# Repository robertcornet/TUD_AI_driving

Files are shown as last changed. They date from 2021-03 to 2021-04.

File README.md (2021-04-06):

# TU Delft AI driving platform
Here you can learn everything about the TU Delft AI driving platform. It is designed for the department of Cognitive Robotics (CoR) at the faculty of 3ME at the TU Delft.

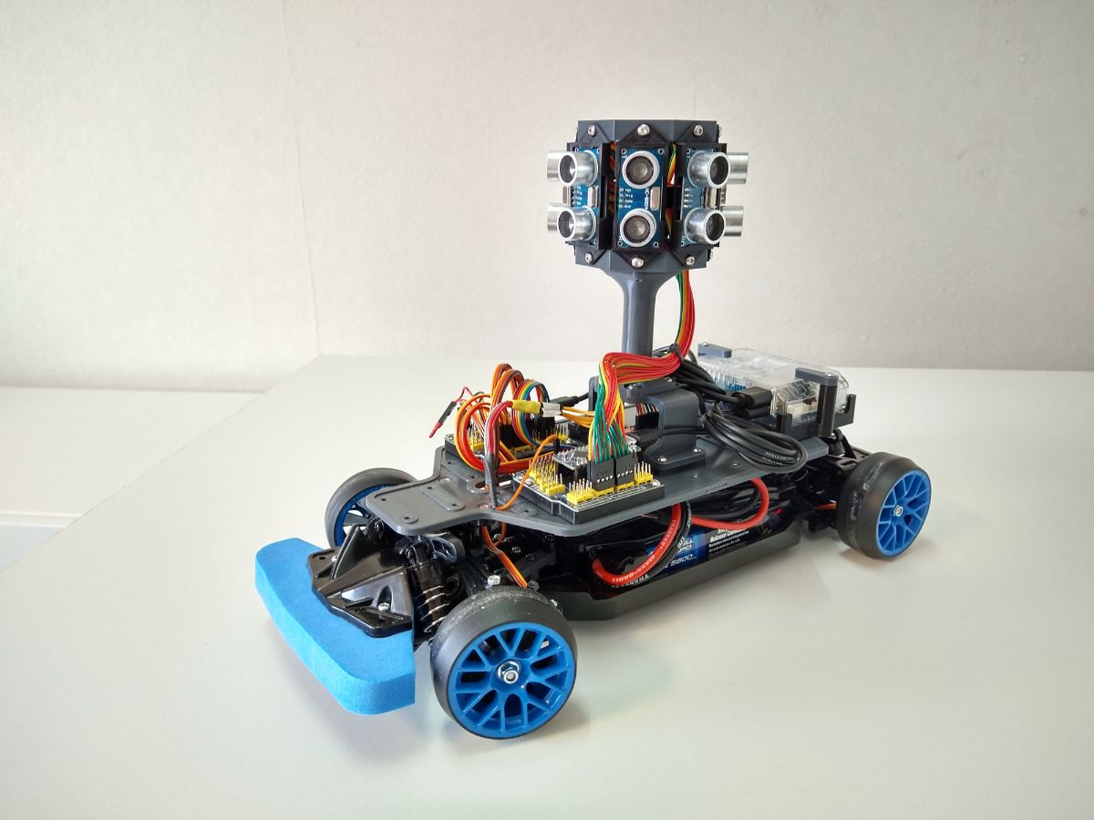
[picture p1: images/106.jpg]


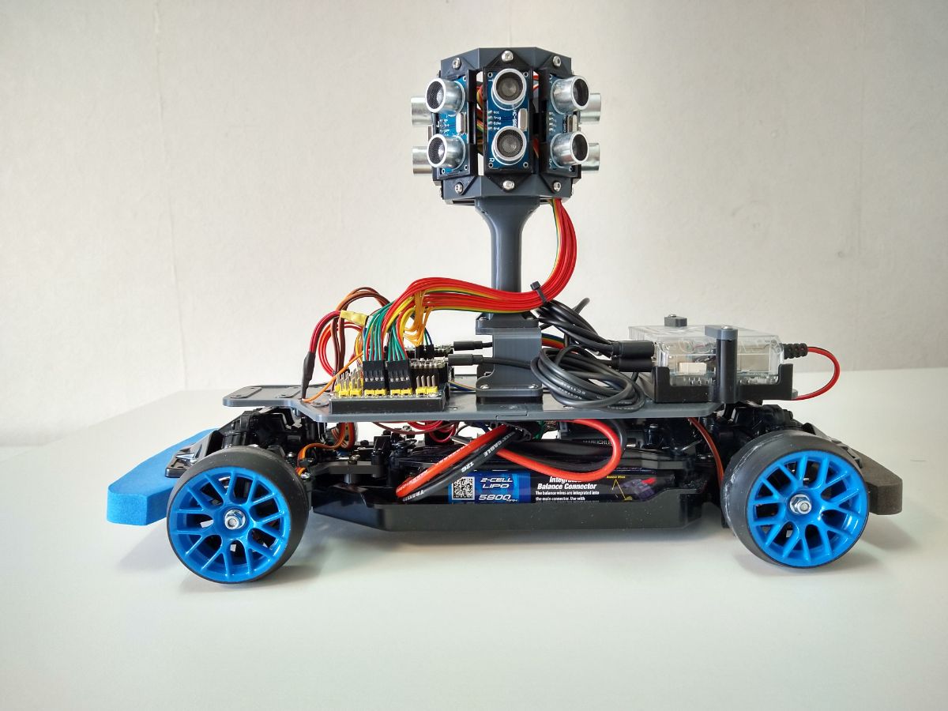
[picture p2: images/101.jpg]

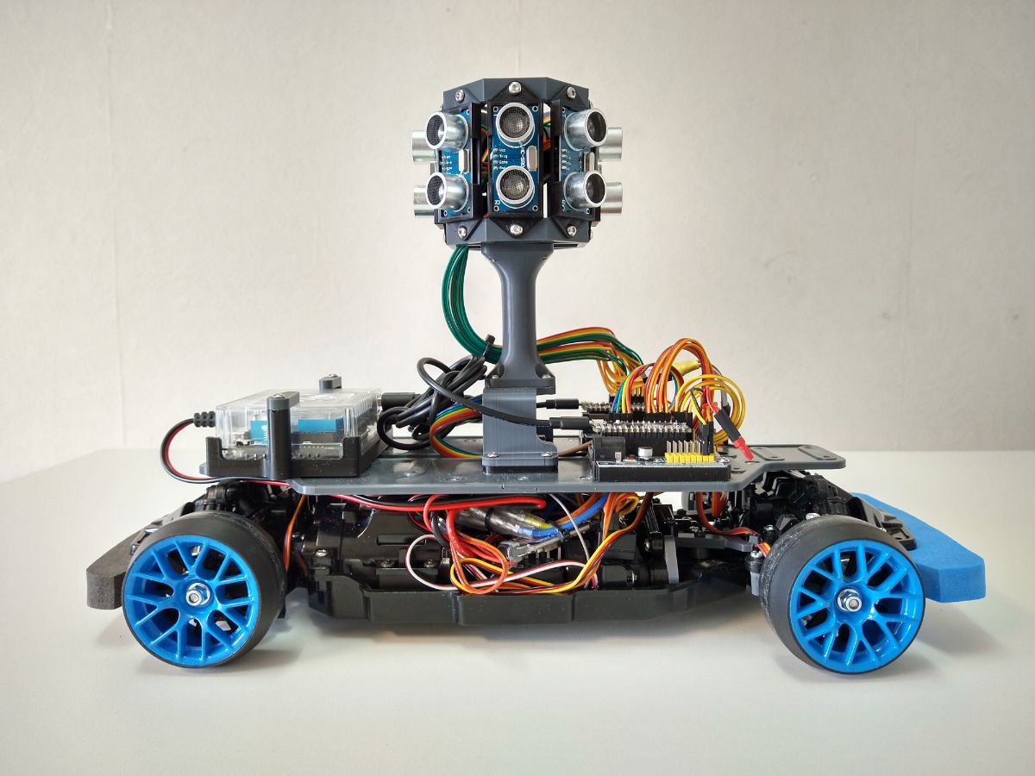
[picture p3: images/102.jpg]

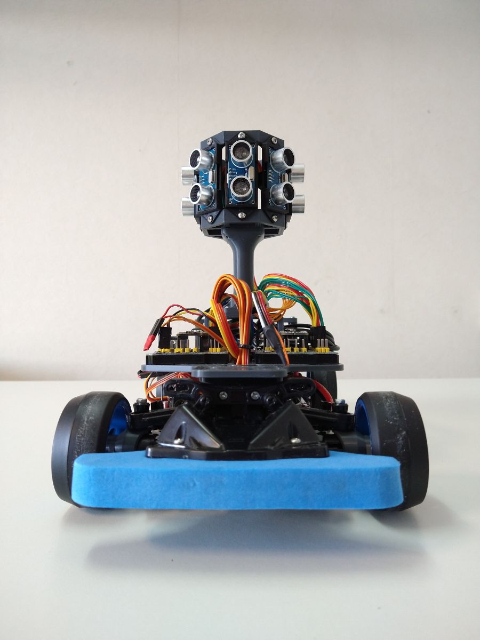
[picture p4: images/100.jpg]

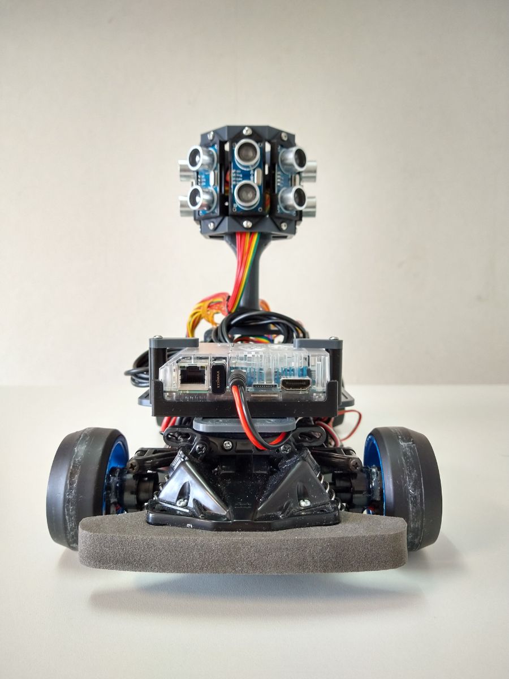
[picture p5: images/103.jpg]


## Who is it for?
This car is designed for very dynamic driving tasks, such as drifting. It can show the unstable behaviour of cars that are pushed to the limit of friction, at low speed and in small spaces. 

With a simple change of tires, you can convert it to a fast (30 km/h) and stable car.

If you are into vehicle research that goes beyond navigation tasks and focusses on dynamic vehicle behaviour and vehicle stability, this platform can be for you. It offers the dynamics of large research platforms on a small scale that requires little space. The onboard accelerometers, gyros and individual wheel speed sensors provide a good basis for developing impressive vehicle controllers.

## What does it offer?
- Low-cost dynamic driving
- Small scale for indoor use
- Access to the relevant vehicle states. (wheel speeds, accelerations, yaw rate)
- Onboard TensorFlow integration for AI development
- Modular platform for easy addition of your own sensors

## Getting Started
- Order everything you need from the [Bill of Materials](/documentation/bill_of_materials.md) 
- Print the [CAD models](/cad)
- Assemble your car with the help of the [Build Guide](/documentation/build_guide.md)
- Install the [Software](/documentation/software_setup.md)

Your platform should now be ready to begin! 
If you want some extra help, check out the [Operation Manual](/documentation/operation_manual.md). If you want to build a vehicle simulation to train your AI, check out the [Simulator section](/simulator).

## See Also
- [BARC](https://github.com/MPC-Berkeley/barc)
- [NVIDIA JetRacer](https://github.com/NVIDIA-AI-IOT/jetracer)
- [AutoRally](https://autorally.github.io/)
- [DonkeyCar](https://www.donkeycar.com/)

## To Do
- Try filtering IMU Data. _The IMU is polled 10-100x faster than the results are published. Try taking the average of all measurements in the publishing interval. _
- Large steering angle mod. _For rear wheel drive drifting, a large steering angle is needed to balance the vehicle in the drift._
- Camera Vision / Lidar module. _The usability of the Ultrasonic sensors is limited._
- Better Inertial Navigation. _Robust algorithm to determine vehicle orientation in space._
- Standstill vehicle rotating bug. _In the simulator, if the vehicle is stationary, it can rotate slowly by steering. This is due to how the slip angles are defined._

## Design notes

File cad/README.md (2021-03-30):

# CAD

The STL files in this folder are meant to be 3D printed. Do not forget to cut the threads for the M3 bolt holes!

The main frame is split into two parts (front and rear) so it can be printed with a smaller printbed.

# Expirimental

In the expirimental folder, you can find the parts that will increase the steering angle from 16.5 degrees (standard) to an average of 29 degrees. 
You can only use this if the front driveshafts are removed.

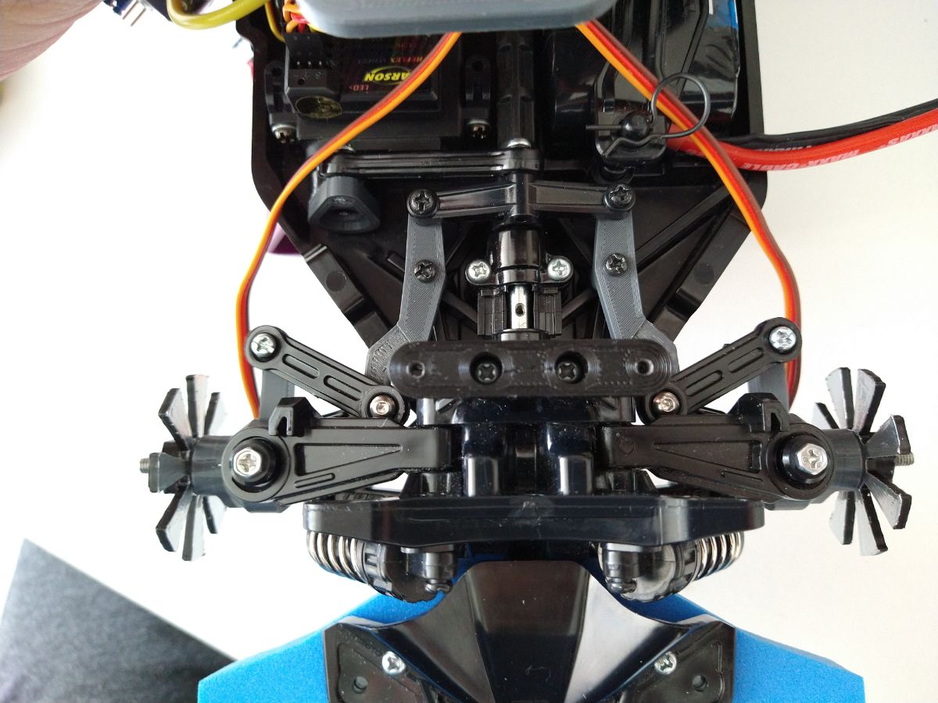
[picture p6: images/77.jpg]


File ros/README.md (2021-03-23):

# How it works
The provided ROS package has very few components. Our network has 3 'nodes', and we can send messages between these nodes.  
- Node 1: This node is on Arduino 1, and sends messages over USB with the topic 'vehicle_state'. It also listens to the messages from Node 3 with the topic 'control_actions'.  
- Node 2: This node is on Arduino 2, and sends messages over USB with the topic 'radar_state'.  
- Node 3: This is the controller that runs on the computer. It listens to Nodes 1 and 2 about the 'vehicle_state' and 'radar_state'. Based on this information, it sends the 'control_actions' to Node 1.

The Arduinos are set to publish a new message with a frequency of 25 hz (40ms interval).

# Setting up your ROS environment
After installing ROS, start by [setting up your own workspace.](http://wiki.ros.org/ROS/Tutorials/InstallingandConfiguringROSEnvironment) The name of the workspace attached is 'tu_ws'.

There are only a few components needed to get the car running. These are:
- custom messages. The vehicle_state_msg and radar_state_msg messages are simple custom messages that tell us what kind of data we can expect on the vehicle_state and radar_state topics.
- launch file: A launch file makes it easy to start multiple processes in one go. We use it to start the two USB connections to the Arduinos.
- script: A script is a function or program we can run on a ROS node. In our case, *controller.py* is the script were we keep our controller.

The above is all captured in a 'package', called *car*.

# TOPICS
vehicle_state
radar_state
control_actions
# MESSAGES

## vehice_state_msg
- float32 u (m/s)
- float32 v (m/s)
- float32 r (rad/s)
- float32 a_x (m/s^2)
- float32 a_y (m/s^2)		
- float32 omega_fl (rad/s)
- float32 omega_fr (rad/s)
- float32 omega_rl (rad/s)
- float32 omega_rr (rad/s)
		
## radar_state_msg
- float32 radar1 (left)(cm)
- float32 radar2
- float32 radar3
- float32 radar4
- float32 radar5
- float32 radar6
- float32 radar7
- float32 radar8 (right)

## control_actions_msg
- float32 steering_action ([-1,1])
- float32 throttle_action ([-1,1])

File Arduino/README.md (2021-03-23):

# Arduino
The sensors on the vehicle are connected to 2 Arduino Nano's. The Arduinos publish the sensor information over USB on the ROS network. They also receive the steering and throttle commands from the ROS network.

## Arduino 1 - Vehicle sensors
The first Arduino is wired to all the vehicle specific sensors:

- Inertial Measurement Unit (IMU)
- Wheel speed sensors (4x)
- 3 Channel RC receiver 

Every 40 milliseconds the sensor information is published on the ROS network.

This Arduino also controls the actuators:
- Steering out (servo)
- Throttle out (esc)

For the Throttle and Steering actions you can switch between two sources:
- Actions from the RC receiver (manual control)
- Actions from the ROS network (automated mode)

## Arduino 2 - Ultrasonic sensors
The second Arduino is for the ultrasonic sensors. There are 2 files included that use the sensors in a different way.

### radar_parallel.ino
In this file, all sensors are triggered at the same time:

> every 40 ms:  
> *publish latest sensor values on ROS network*    
> *trigger all sensors simultaneously*

### radar_sequential.ino
In this file, a sensor is triggered after the previous sensor is finished:

> trigger sensor n  
>   
> *if* (response received or timeout expired (no response received)){  
>      *trigger sensor n+1*  
> }

> every 40 ms:  
> *publish latest sensor values on ROS network*

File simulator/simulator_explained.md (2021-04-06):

# Vehicle motion simulator

The simulator can be used to develop and test your controllers. From the two inputs (Steering and Throttle), it will approximate how the car would behave. The simulator is built in the [OpenAI GYM](https://gym.openai.com/) structure.

The simulator is used in combination with the Reinforcement Learning programs from the [RLControlTheoreticGuarantee Github](https://github.com/RLControlTheoreticGuarantee/Guarantee_Learning_Control). 

Inluded on this page is a folder with an older copy of that github, including the vehicle simulator. 
If you follow their installation guide, you can download the folder above and start training immediately.

## Using the simulator
- Define your objective and what states you can observe in your experiment. Make sure your controller does not rely on states that you can not observe in the real world!
- Choose the time step for the agent (eg, 10 hz, 25hz, etc). The vehicle simulation updates at 1000hz for stable integration. 
- Define how you want an episode to start (*def* reset) and when to end (*done*)
- Construct your reward so it promotes the desired behaviour

## States
In the simulator you have access to the following vehicle states:

- longitudinal velocity *u*
- lateral velocity *v*
- yaw rate *r*
- longitudinal acceleration *a<sub>x</sub>*
- lateral acceleration *a<sub>y</sub>*
- wheel rotation velocities *Ω* 

Additionally, you can generate environment borders: \
- As a random racetrack
- As a square room

These borders can be detected with a 'lidar' simulation.

## Primary Simulator Functions
The most important functions are:

*def* \_\_init\_\_()\
Here all the parameters are set for the car and the environment. For example, here you would change the mass, the dimensions, or the motor characteristics of the car. This is also were you set if your car is 4wd or rwd, and how large the time steps of the simulation will be.

*def* reset()\
This function is called at the beginning of every training episode. It (re)sets the parameters for the episode. Here you can set how and where your vehicle starts in the environment. It can also be used to build a different enviroment for every episode.

*def* step()\
This is the main simulation function. It takes two inputs (steering and throttle), and runs the simulation for one step in the environment.  
It returns the new state of the car and environment, and a reward based on that state. 

## Secondary Simulator functions

*def* render()\
When eval_render == True in variant.py, this function is called every step. It draws the car and the environment.

### Motor and ESC
*def* ESC()\
This function simulates the behaviour of the electronic speed controller (ESC) included in the Tamiya kit (TBLE-02S).\
The ESC puts out a voltage to the motor depending on the input signal. The input is a PWM signal with pulses between 1000us (full throttle) and 2000us (full braking). This behaviour is modelled in the simulator as a voltage multiplier; the ESC acts as a multiplier in range [0-1] between the battery voltage and motor.\
The folling values were measured by experiment:

|Throttle %|Voltage Mult.|
|---|---|
|0|0|
|7.5|0|
|7.6|0.44|
|10|0.53|
|20|0.75|
|30|0.84|
|40|0.89|
|50|0.94|
|60|0.96|
|70|1|
|80|1|
|90|1|
|100|1|

*def* motor()\
This function calculates the torque that the motor will produce, given the voltage from the ESC and its rotational speed.

Tamiya specifies a motor RPM per volt (KV) of 2222, and a stall torque per volt (TV) of 0.0042 Nm. Our measurements revealed a KV closer to 2775, and a TV of 0.0065 Nm.

|Voltage|Motor RPM|KV|
|---|---|---|
|3.45|9322|2702|
|4.09|11376|2781|
|5.82|16116|2769|
|6.57|18179|2765|
|6.95|19276|2774|
|7.30|20540|2813|
|7.48|20935|2798|
|7.79|21725|2789|

### Tires
TIRE_FLUCTUATION is an array of 4 values. It can be used to add a little noise on the tire behaviour of the individual wheels, that changes from episode to episode.

### LIDAR
*def* lidar_get_state()\
Returns the distance to the walls at the angles set in SENSOR_ARRAY (*def* \_\_init\_\_()).\
*def* lidar_get_state() calls *def* lidar_rayDist(). There the distances can be checked in two different ways:
1. To the walls of a room (self.track__center)
2. To the 'walls' of a race track (self.track_left, self.track_right)\
Both options are quite different, make sure to uncomment the right one!

### Room generation
*def* gen_room()\
Very simple function that generates a square room given a length and width in meters. It returns the x,y-coordinates of the corners.

### Track generation
*def* track_generator()\
Generates a random track. It is adapted from the methods discussed [here](http://blog.meltinglogic.com/2013/12/how-to-generate-procedural-racetracks/)

*def* track_check_valid()\
Checks if the generated random track is 'valid'. If a track has 'kinks' in the corners, the track will be 'invalid'. 

## Expirimental, not recommended.

### Car following, leading car
These functions are for running a leading car. You can use it to train your AI to follow a car using lidar or ultrasonic sensing.

*def* initialize_leading_car()\
Initializes the leading car in a random position in front of your own car.

*def* run_leading_car()\
Chooses the actions for the leading car. Limits for the speed, acceleration and yaw rate of the leading car are set in this function.

*def* get_radar_state_zones()\
This function tries to simulate how an ultrasonic sensor would see the leading car in practice. If the leading car is within the FOV of a sensor, it returns the distance between the two cars.  

## See also
For more details of the vehicle motion simulation, refer to Chapter 2 of [this Thesis](https://repository.tudelft.nl/islandora/object/uuid%3A7bedb60a-ced8-4fcf-97ca-80208861a413)

# Learning Algorithms
With the included software, you can train your AI using Soft Actor Critic (SAC) and Lyapunov-based Soft Actor Critic (LSAC). Only the most basic settings will be discussed here.

variant.py\
Here you choose your environment, learning algorithm and training times. You can also set if you want to render the environment. 

main_for_sac.py\
This is the function you will run every time you want to start training or evaluating.

/LSAC/LSAC_V1.py\
Here you can change the dimensions of the neural networks. Change the following lines:
- lines 305/306
- lines 340/345
- lines 351/356

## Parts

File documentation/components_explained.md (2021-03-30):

# Componenents Explained

This page explains the choice of individual components, as well as how they are used, and what can be improved.

## The wheel speed sensors 
The rotational velocity of the wheels is important information when vehicle dynamics are considered. It is often the only measurement we have of the interface between the vehicle and the road.
It can be used to determine the velocity of the vehicle (from the non-driven wheels) or to estimate the longitudinal slip of the driven wheels.

Conventionally, wheel speeds are measured with hall sensors and a magnetic ring. This is also the method used on a large research platform such as the [AutoRally project](https://autorally.github.io/).

In our case, the rotational velocity is measured with IR-reflectance sensors. A small IR transmitter and receiver board is mounted on each wheel hub. A disk is mounted inside the wheels with aluminium tape to reflect the IR light. The gaps in the disk obviously do not reflect light, generating a square wave signal when the wheel is rotating.

IR-reflectance sensors can typically be bought in a **'Digital'** or **'Analog'** version. 
A digital sensor determines the reflectivity of a surface by pulling a voltage to 'HIGH', and counting how long it takes to discharge a small capacitor due to the amount of light reflected. This is a very slow process, and this gives no information about when the surface switches from 'light' to 'dark'. 

A much better solution is to use an **Analog** version of the board. An analog board puts out a voltage as a function of the reflected light. Since we are only interested in 'light' or 'dark', we can read the sensor with a **DIGITAL** pin on the arduino. Whenever the surface switches from **'light' to 'dark',** the voltage switches from **HIGH to LOW**, and an Interrupt routine is called to note the time of the switch.

Other projects use encoder disks with a black and white pattern to create a 'light' and 'dark' surface. This is not sufficient; a dark colored surface can still reflect IR light. A much more robust 'dark' surface is a surface that is sufficiently far away, regardless of color. Therefor a robust solution was found in using 'slotted' encoder disks.

An analog board with a **47k** resistor works best. Boards with a lower resistance will not reliable pull the voltage low enough to trigger Arduino's Digital LOW threshold.

## IMU

The vehicle is equiped with a low-cost 9-dof IMU:[SparkFun 9DoF IMU Breakout - ICM-20948](https://www.sparkfun.com/products/15335). 

This is used to measure the longitudinal and lateral accelerations.
The accelerations are measured in a plane perpendicular to gravitation vector. The orientation of the board is determined by a switching filter. This compensates the drift of the gyros and the noise of the accelerometers.

### Switching Filter	
If no motion is detected for a certain amount of time, the board is assumed to be stationary.
If the board is stationary; the orientation is determined by a weighted sum between the Accelerometers and the Gyrometers:

alpha = 0.95*(Gyro)+0.05*(Accel.)

When the board is in motion, the accelerometer data can no longer be used to accuratelyseperate the direction of the gravitational vector and the specific motion of the board. The angle is then solely determined by the Gyrometers:

alpha = 1.0*(Gyro)

### Inertial Navigation
The longitudinal and lateral velocity can be obtained by integrating the measured accelerations. In practice the usability of the calculated velocities is extremely limited. The calculated values are transmitted on the ROS network, but it is recommended that they should not be trusted.

## POWER
Power is supplied to the odroid with a 6 amp BEC(battery Eliminating Circuit). This is a common component in the RC hobby. Alternatively any DC/DC converter buck can be used that outputs 5V at 4+ A.

## Batteries
Power is provided to the car with Traxxas Lipo Batteries. They are very common, and easy to charge and maintain with plug and play chargers.

Do not let the voltage get too low. The vehicle will drain the battery completely if it is not disconnected. The battery monitor on the vehicle provides a reference for the voltage. If the voltage gets too low, the alarm will sound. 
The individual cell voltage can not be measured, only the sum (total voltage) is valid.

## Ultrasonic sensors
Ultrasonic sensors are used as a cheap way to observe the environment as an alternative to using camera vision. 

The vehicle can be equipped with a number of ultrasonic sensors in different configurations. The intention was to use ultrasonic sensors as a low cost alternative to lidar sensors. However, in testing it turns out that the usability of ultrasonic sensors is limited:

1. If the sensor is not pointing perpendicular to the surface it is supposed to measure, the sound waves will not bounce back to the receiver and the surface will not be observed correctly.

2. The relative slow speed of sound means that the sensors can not be polled at rates over 30hz. Normally, each sensor is polled individually, and the next sensor in the array is polled only after the first has received its echo (or has timed out). This would slow the update rate down to unusable levels for multiple sensors. 

3. The sensors have a fairly wide, and not always consistent FOV. This means that a sensor will pick up any object in its FOV, not only the distance straigth ahead.

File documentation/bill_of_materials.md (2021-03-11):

# Bill of Materials

## Car, ~€230
| Component| Quantity | URL | Notes |
| --- | --- | --- | --- |
|Tamiya TT-02 Chassis |1| [Conrad](https://www.conrad.nl/p/tamiya-tt-02-toyota-gazoo-yaris-wrt-brushed-110-rc-auto-elektro-straatmodel-4wd-bouwpakket-1876796) | |
|Steering Servo |1|[Conrad](https://www.conrad.nl/p/hitec-standaard-servo-hs-311-analoge-servo-materiaal-aandrijving-polyamide-stekkersysteem-jr-209893)| |
|3ch Tx/Rx combo|1|[Conrad](https://www.conrad.nl/p/carson-modellsport-reflex-wheel-start-rc-pistoolzender-24-ghz-aantal-kanalen-3-incl-ontvanger-1920203) | |
|Drift wheels|1|[Conrad](https://www.conrad.nl/p/reely-110-straatmodel-complete-wielen-drift-y-spaken-groen-1-stuks-2226537)| |
|TT-01 Foam Front bumper|1|[Conrad](https://www.conrad.nl/p/tamiya-53683-reserveonderdeel-bumper-1498380)|Optional|
|Battery Cable + Connector|1|[Conrad](https://www.conrad.nl/p/accu-kabel-1x-trx-stekker-1x-open-kabeleinde-3000-cm-40-mm-modelcraft-208481)|Use a connector that matches your batteries|

## Charger and Batteries, ~€150
| Component| Quantity | URL | Notes |
| --- | --- | --- | --- |
|Traxxas EZ-Peak 4a charger|1|[Conrad](https://www.conrad.nl/p/traxxas-ez-peak-plus-4a-multifunctionele-modelbouwlader-100-v-230-v-4-a-1969902)| |
|Traxxas 5800 mah 2s LiPo battery|1+|[Conrad](https://www.conrad.nl/p/traxxas-lipo-accupack-74-v-5800-mah-aantal-cellen-2-25-c-box-hardcase-traxxas-id-1432751)||

## Computer, ~€200
| Component| Quantity | URL | Notes |
| --- | --- | --- | --- |
|Odroid XU-4|1|[Antratek](https://www.antratek.nl/odroid-xu4-octa-core-computer-with-samsung-exynos-5422)| |
|Odroid XU-4 Case|1|[Antratek](https://www.antratek.nl/odroid-xu4-case-clear)| |
|Power Supply 5v 4a|1|[Antratek](https://www.antratek.nl/power-supply-5v-4a)|For using the computer on wall power|
|Odroid XU4 eMMC storage 64GB|1|[Antratek](https://www.antratek.nl/64gb-emmc-module-h2) | |
|eMMC to microSD adapter|1|[Antratek](https://www.antratek.nl/emmc-module-reader)| |Used only for flashing the OS|
|Odroid XU4 Real-Time-Clock battery|1|[Antratek](https://www.antratek.nl/rtc-backup-battery) | |
|USB Wifi Module|1|[Conrad](https://www.conrad.nl/p/edimax-ew-7611ulb-wifi-stick-usb-20-wifi-bluetooth-150-mbits-1491083) |Different Wifi modules are fine|
|DC-DC Stepdown Converter|1|[Conrad](https://www.conrad.nl/p/master-bec-spanningsregelaar-6-25-v-6-a-1435726)|Any 5v 4a+ DC-DC converter should work|
|5.5mm/2.1mm barrel connector|1|[Conrad](https://www.conrad.nl/p/voltcraft-laagspannings-aansluitkabel-laagspanningsstekker-open-kabeleinde-55-mm-21-mm-200-m-1-stuks-749123)| |

## Sensors, ~€65
| Component| Quantity  | URL | Notes |
| --- | --- | --- | --- |
|IMU|1|[Antratek](https://www.antratek.nl/9dof-imu-breakout-icm-20948-qwiic)| |
|QTR-1A Reflectance Sensor (2-Pack) Pololu 2458 |2|[VeM](https://www.vanallesenmeer.nl/QTR-1A-Reflectance-Sensor-(2-Pack)-Pololu-2458)|Need 4 sensors |
|Ultrasonic Sensors|(8)|[Antratek](https://www.antratek.nl/hc-sr04-ultrasonic-sonar-distance-sensor)||

## Arduinos, ~€40
| Component| Quantity | URL | Notes |
| --- | --- | --- | --- |
|Arduino Nano Every|2|[Antratek](https://www.antratek.nl/arduino-nano-every-with-headers) | |
|Arduino Nano sensor I/O shield v3.0|2|[VeM](https://www.vanallesenmeer.nl/Arduino-Nano-sensor-I/O-shield-v3.0) | |
|USB A to Micro B cable|2|[Conrad](https://www.conrad.nl/p/realpower-usb-20-aansluitkabel-1x-micro-usb-1x-micro-usb-stekker-6000-cm-zwart-2304825)] |>15 cm|

## Wiring, ~€200

| Component| Quantity | URL | Notes |
| --- | --- | --- | --- |
|Short 3pin connector cable|3|[Antratek](https://www.antratek.nl/3-pin-10-extension-cable)|Receiver to Arduino, >15cm|
|Long 3 pin connector cable|4|[VeM](https://www.vanallesenmeer.nl/Servo-Verlengkabel-RC-Futaba-JR-Man-vrouw-50-cm) |Wheel speed sensors, >50cm |
|4 pin connector cable|8|[Antratek](https://www.antratek.nl/jumper-wire-0-1-4-pin-12) |1 cable per Ultrasonic sensor |
|3 pin extension cable|3 |[Conrad](https://www.conrad.nl/p/modelcraft-servo-verlengkabel-1x-jr-stekker-1x-jr-bus-2500-cm-014-mm-plat-223733) |voltage monitoring(2x) + ESC to Nano extension|
|30cm m-m jumper cables|1 pack|[Conrad](https://www.conrad.nl/p/makerfactory-jkff40-jumper-kabel-arduino-banana-pi-raspberry-pi-40x-draadbrug-bus-40x-draadbrug-bus-3000-cm-bont-1970438) | IMU to Nano, 6 wires|

## Optional/comsumables
| Component| Quantity | URL | Notes |
| --- | --- | --- | --- |
|M3 screw assortiment||[Conrad](https://www.conrad.nl/p/thicon-models-20093-schroef-1-sets-1669366)| | 
|M2x4-6 screws || [Conrad](https://www.conrad.nl/p/toolcraft-m2-x-6mm-to-5661774-cilinderschroeven-m2-6-mm-binnenzeskant-inbus-din-912-iso-4762-staal-100-stuks-1887258) |4 needed for mounting wheel speed sensors|
|Shrink tube assortiment| | | |
|5-50k resistors |2x | |Splitting battery voltage for voltage monitor |

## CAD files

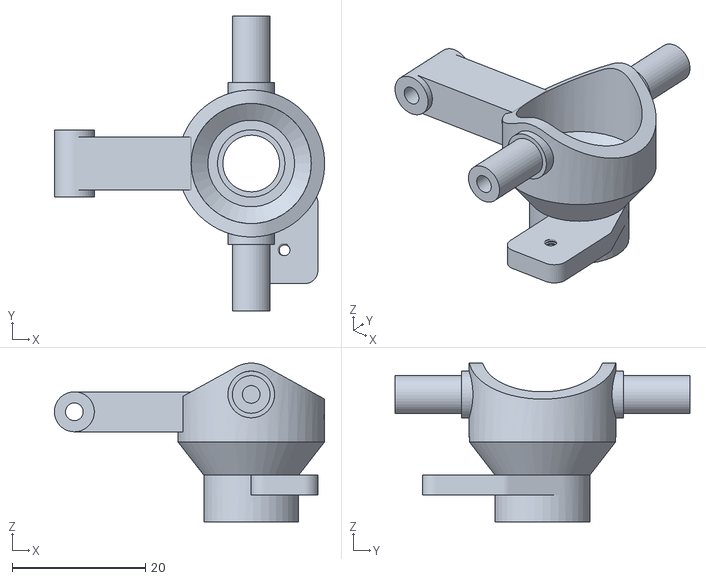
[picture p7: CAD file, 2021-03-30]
cad/expirimental/(expirimental)wheelhub_fl.STL
40.5 x 44.2 x 23.8

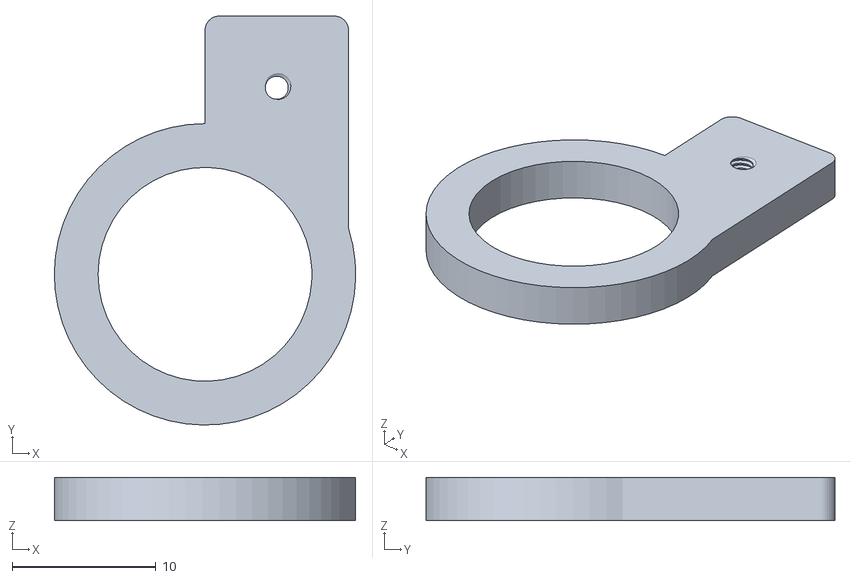
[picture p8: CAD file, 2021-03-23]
cad/wheel_encoder_sensor_mount(4x).STL
21.0 x 28.5 x 3.00

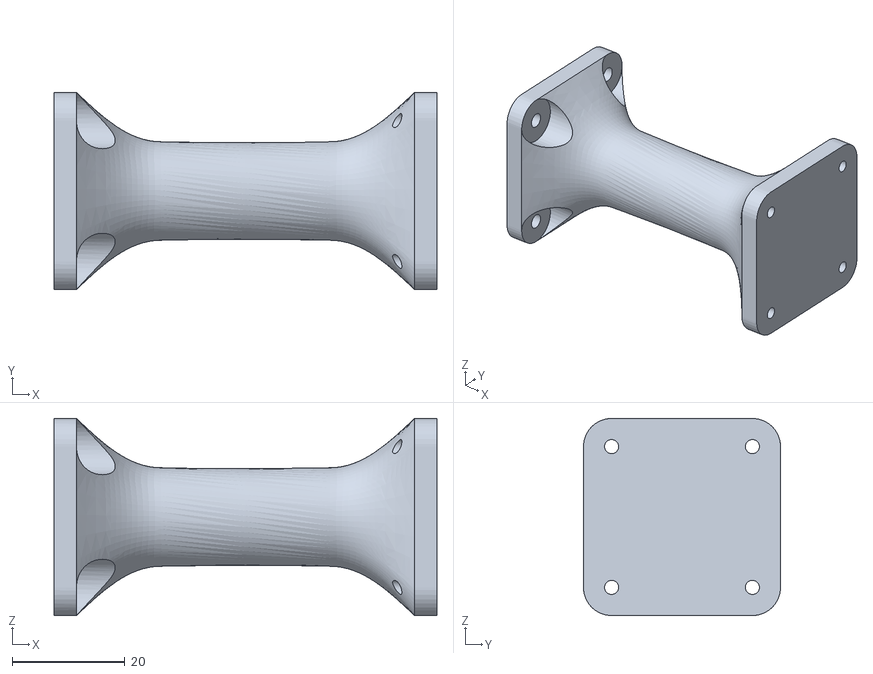
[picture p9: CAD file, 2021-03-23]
cad/ultrasonic_raiser.STL
68.0 x 35.0 x 35.0

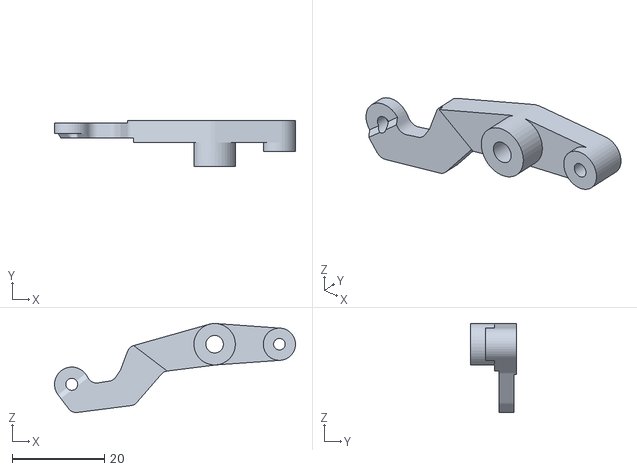
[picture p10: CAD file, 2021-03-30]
cad/expirimental/(expirimental)steering_arm_right.STL
52.3 x 10.0 x 19.3

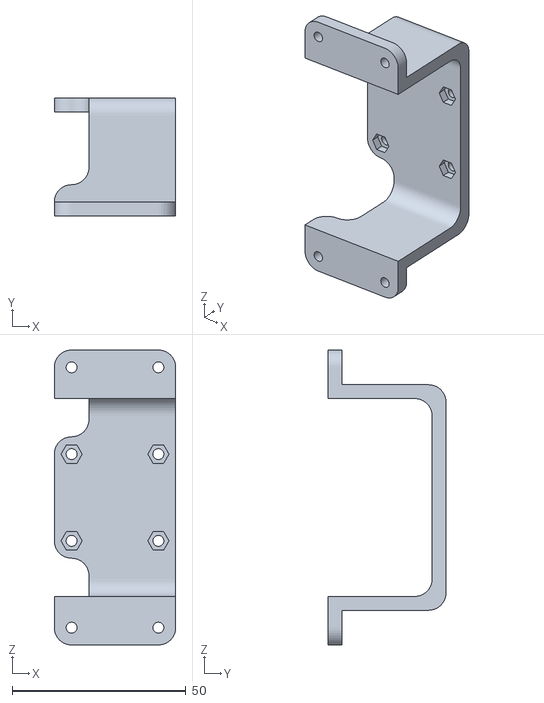
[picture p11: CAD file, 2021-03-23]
cad/ultrasonic_base.STL
35.0 x 34.0 x 85.0

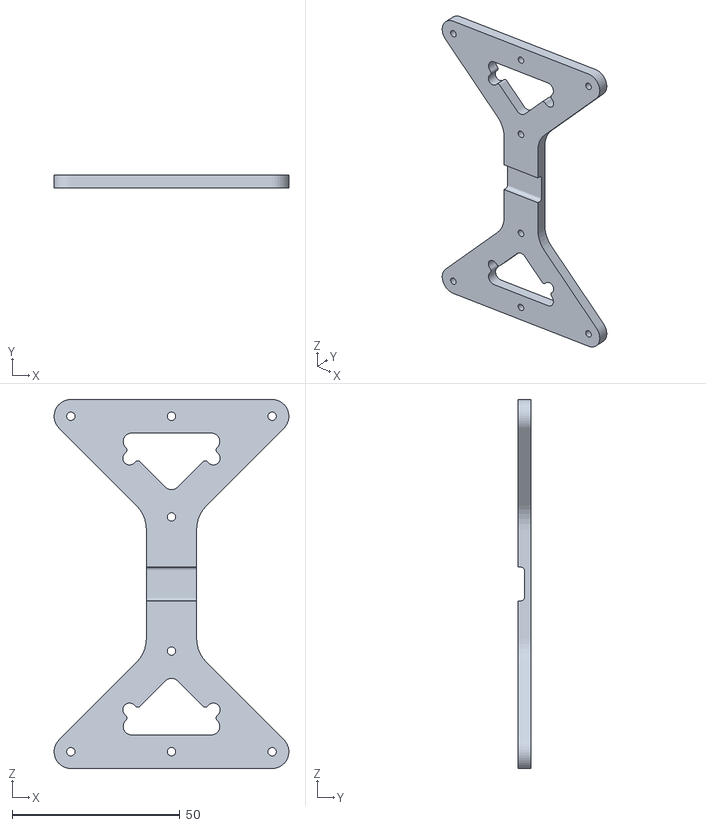
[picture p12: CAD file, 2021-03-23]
cad/frame_center_brace.STL
70.0 x 4.00 x 110.0

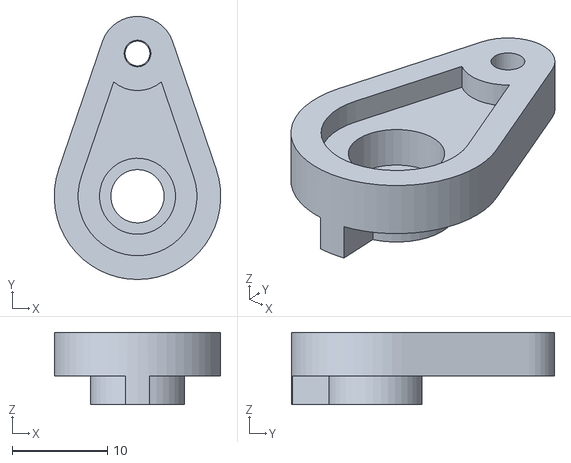
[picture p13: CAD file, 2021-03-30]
cad/expirimental/(expirimental)servo_arm_15mm.STL
17.5 x 27.6 x 7.60

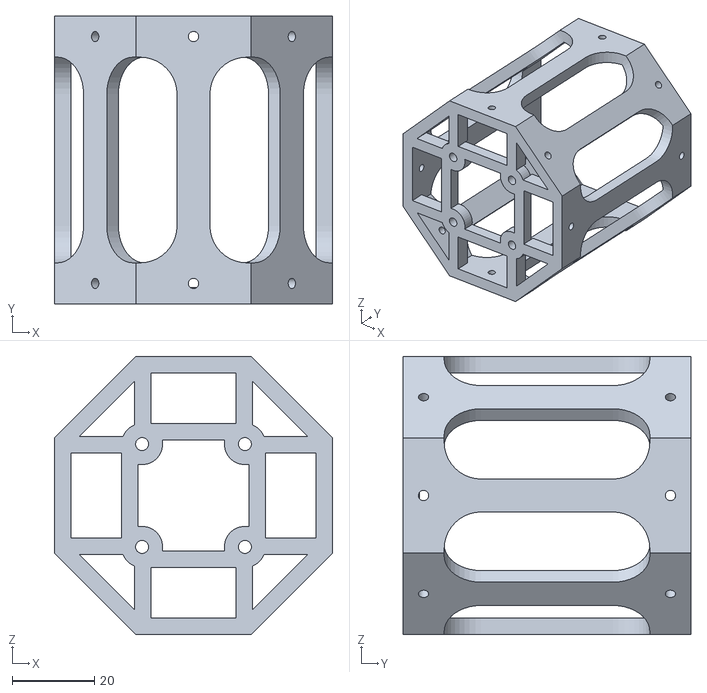
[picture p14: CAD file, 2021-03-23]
cad/ultrasonic_top_cage.STL
67.6 x 70.0 x 67.6

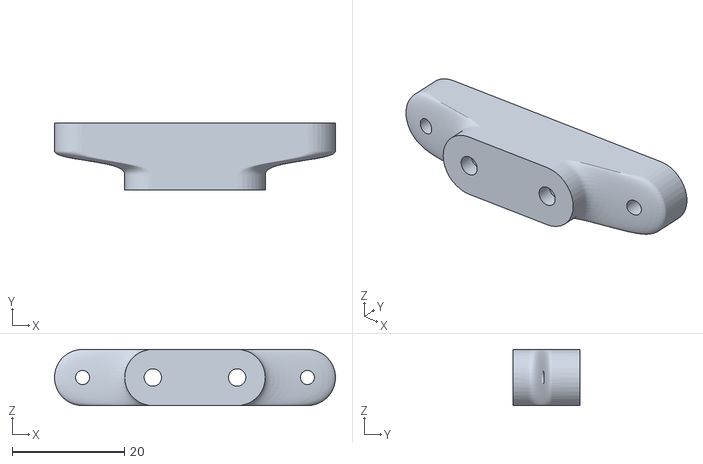
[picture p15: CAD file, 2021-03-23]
cad/frame_mount(2x).STL
50.0 x 12.0 x 10.00

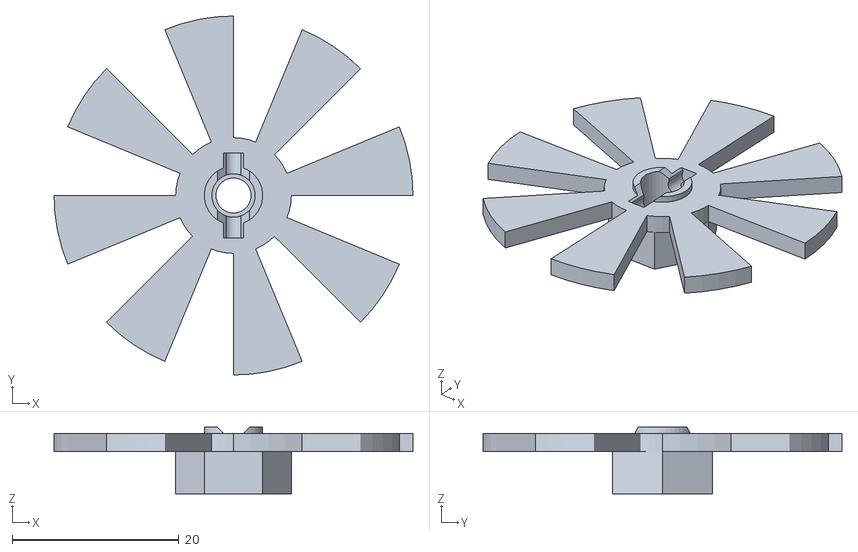
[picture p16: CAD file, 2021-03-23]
cad/wheel_encoder_8slots(4x).STL
43.0 x 43.0 x 8.00

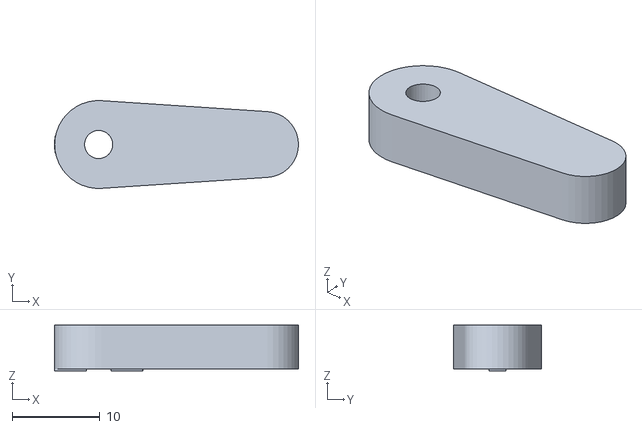
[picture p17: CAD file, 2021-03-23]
cad/odroid_bumper_lock(2x).STL
27.8 x 9.98 x 5.20

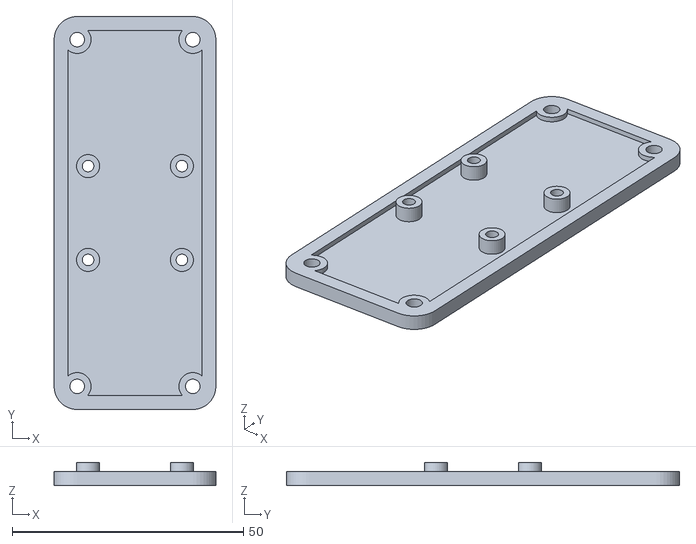
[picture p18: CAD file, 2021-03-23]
cad/imu_mount_plate.STL
35.0 x 85.0 x 5.00

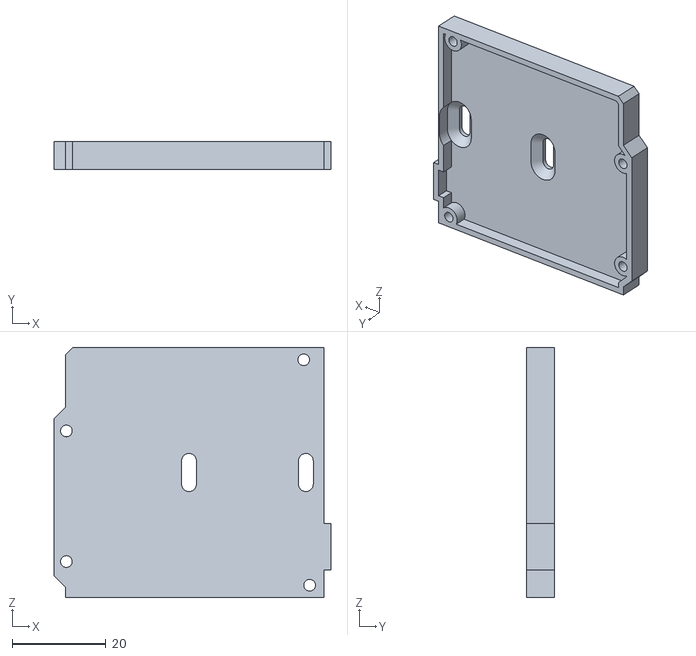
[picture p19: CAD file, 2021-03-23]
cad/arduino_nano_bumper.STL
59.2 x 6.00 x 53.5

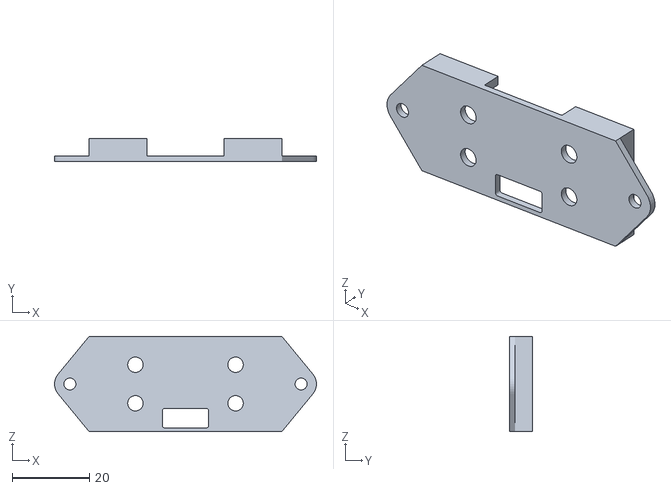
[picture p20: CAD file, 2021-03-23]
cad/ultrasonic_sensor_case.STL
68.0 x 6.00 x 24.8

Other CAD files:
cad/expirimental/(expirimental)wheelhub_fr.STL
cad/expirimental/(expirimental)steering_arm_left.STL
cad/odroid_bumper.STL
cad/frame_plate_front.STL
cad/frame_plate_rear.STL

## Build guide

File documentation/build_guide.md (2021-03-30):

# Build Guide

This document will guide you through the build process of the vehicle. Get your tools and materials ready and build along!
If you have questions about the choice of components, refer to [here](/documentation/components_explained.md).

### Required skills
- Soldering servo wires, header pins and battery connectors
- Basic assembly skills
 
### Required tools and materials
- Set of Phillips-style screwdrivers
- 2mm Hex screwdriver
- Access to a 3D-printer or 3D-print service
- Knife, scissors, wire stripping tools
- Hot glue gun
- M3 thread cutting tool
- Soldering iron
- Adhesive aluminium foil/tape or IR-reflective tape
- Small zip ties

# Part 1: The Chassis
Start by building the TT-02 chassis with the help of the included instructions. Use the included foam bumper (black) in the rear, and the  optional TT-01 bumper (blue) in the front. 

Connect the motor:\
blue - green\
yellow - yellow\
orange - \[-\]  

Your vehicle should now look similar to this:

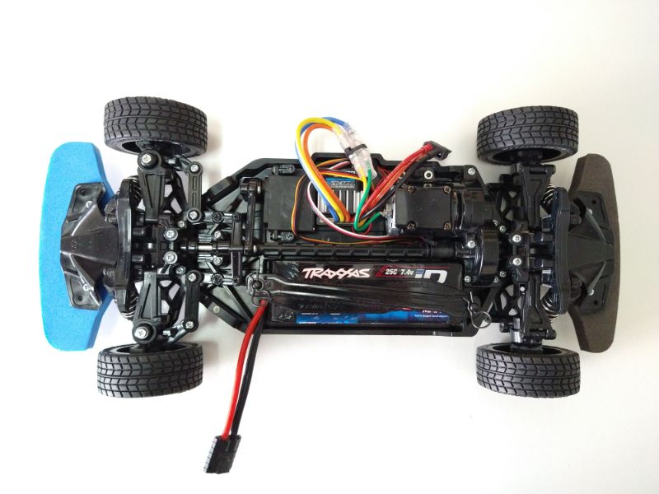
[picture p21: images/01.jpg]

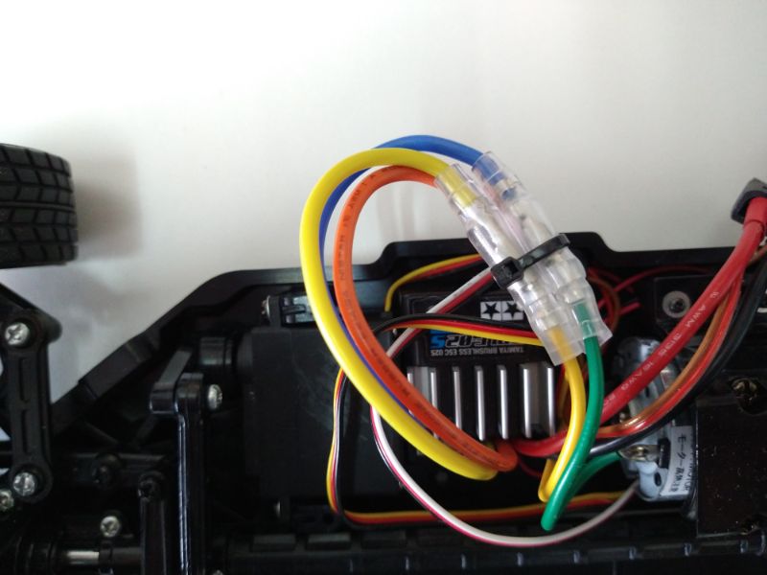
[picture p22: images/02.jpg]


# Part 2: Battery Power Wiring
The power from the battery is split to the Vehicle Electronic Speed Controller (ESC) and the DC-DC step down to power on-board computer. We will also add a third connector so we can monitor the battery voltage. The auxiliary connector is a standard servo wire with the signal wire removed:

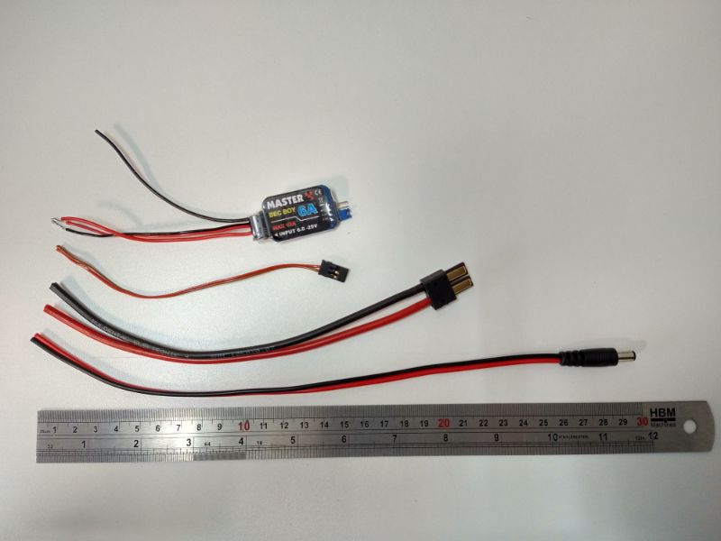
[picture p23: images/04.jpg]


Cut the Tamiya connector off the ESC, and wire in the DC-DC converter, the battery connector and the auxiliary port.

Solder the wires in parallel and pay attention to the polarity of the components. Leave about 15cm of battery wire. Cover the wires with heat shrink tube (remember to put it in place before soldering the wires together). This protects the exposed wires from shorting and provides strain relief for the smaller wires:

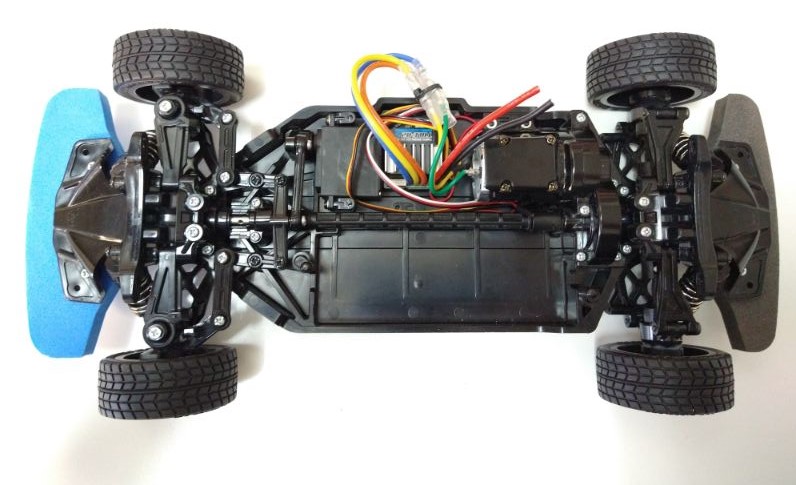
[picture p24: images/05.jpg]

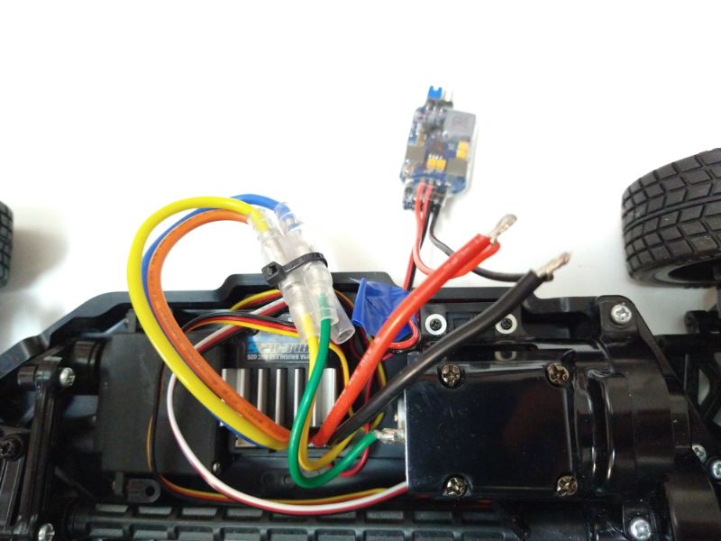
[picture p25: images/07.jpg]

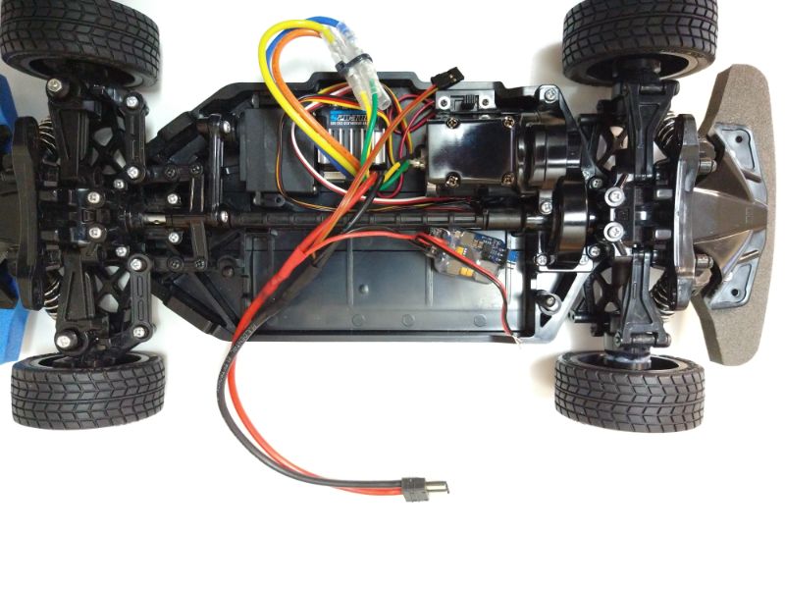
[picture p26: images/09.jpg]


Solder the barrel connector to the output of the DC-DC step down converter. **Make sure the output is set to 5 volts!**

# Part 3: The Mounting Plate
The holes in the 3d printed parts are not threaded yet. It is recommended to run a tap trough the holes first. The holes are sized for M3x0.5 threads.

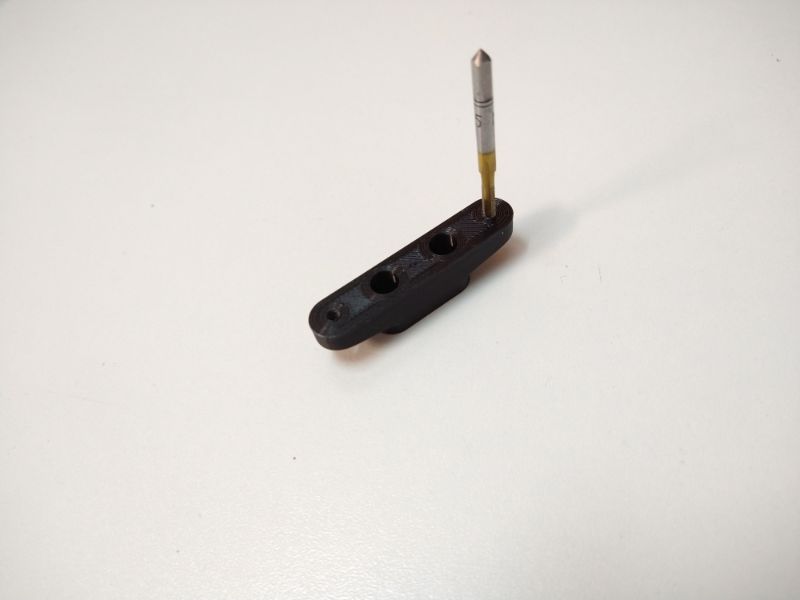
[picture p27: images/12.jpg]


The threads in the upper deck are intended to be reused frequently, and therefor made with m3 nuts. The hexagon cutouts are slightly undersized. The nuts can be pressed in the deck, but it is recommended to use a little bit of heat to soften the plastic. This can be done with a soldering iron on low heat. Heat the nut until the plastic starts to soften and the nut sinks into the deck. This should only take 5~10 seconds on 250-300 C.  Quickly remove the heat source, turn the part around and press it on a flat surface for a few seconds. This way, the nuts will sit flat and square:

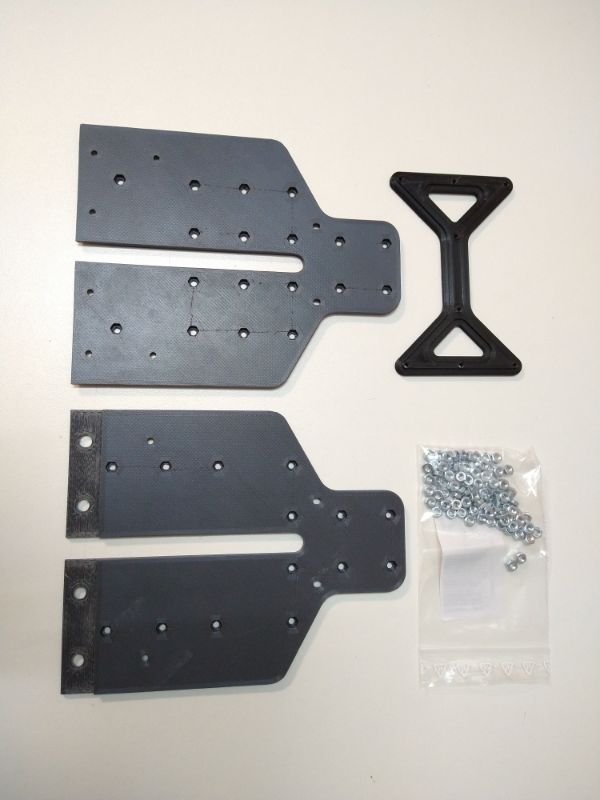
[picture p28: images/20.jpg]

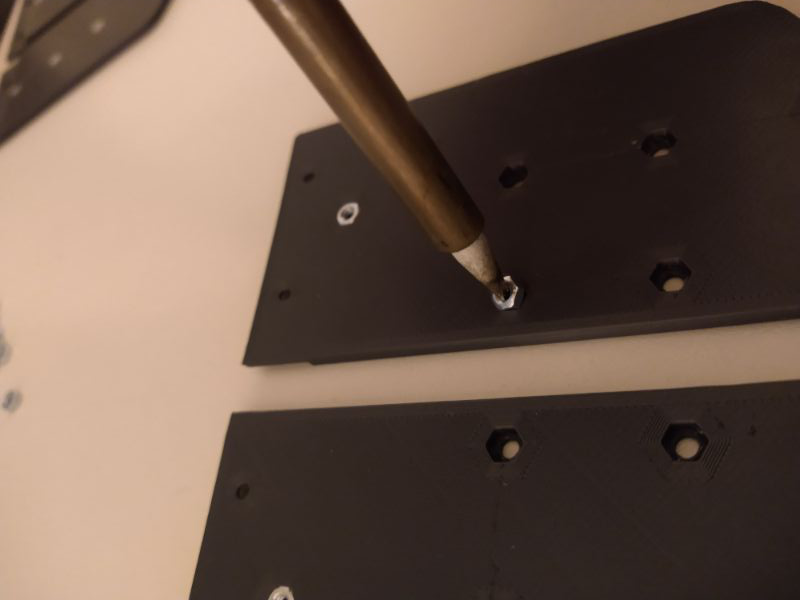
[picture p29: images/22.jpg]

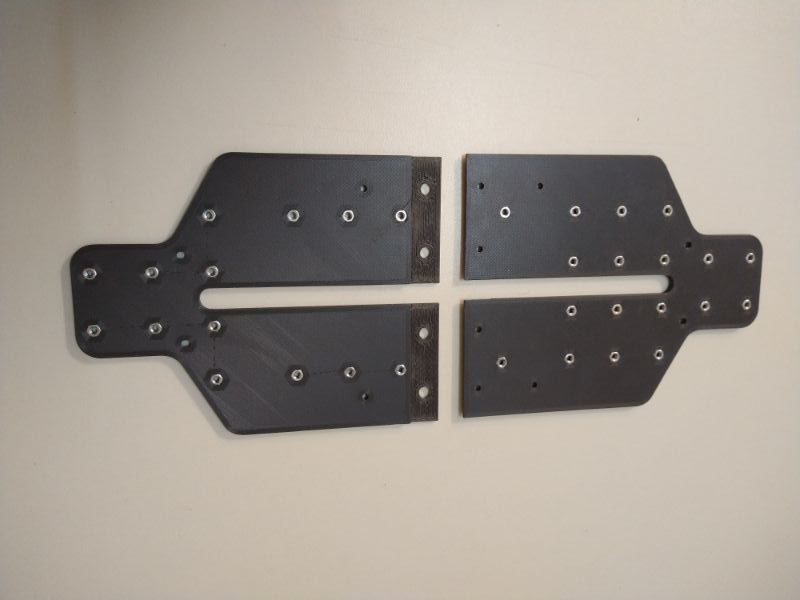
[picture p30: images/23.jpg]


Remove the screws on the front and rear bulkhead and use them to mount the deck supports:

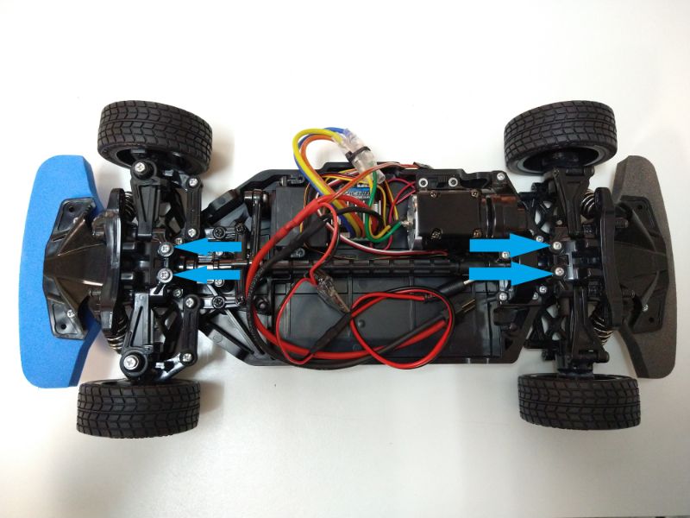
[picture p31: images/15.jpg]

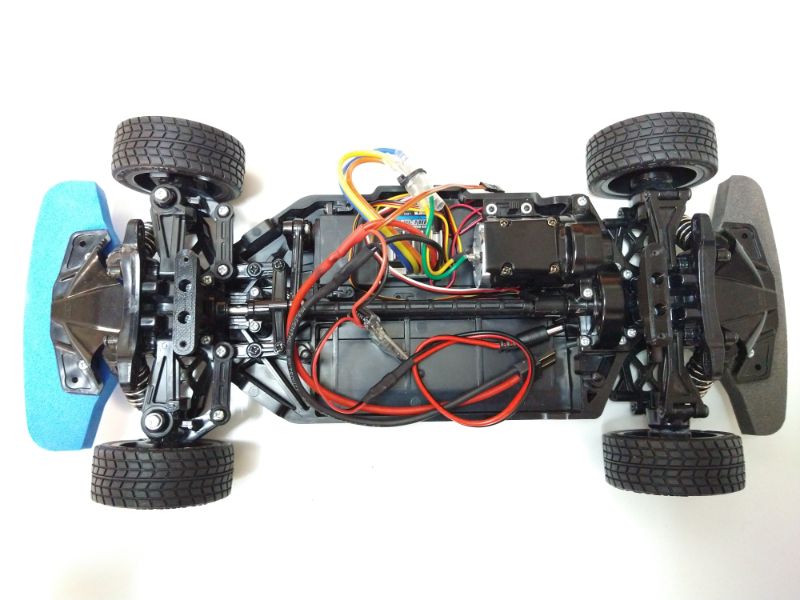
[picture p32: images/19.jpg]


Mount the deck brace to the underside of the front and rear deck plates, and mount the combined deck to the deck supports:

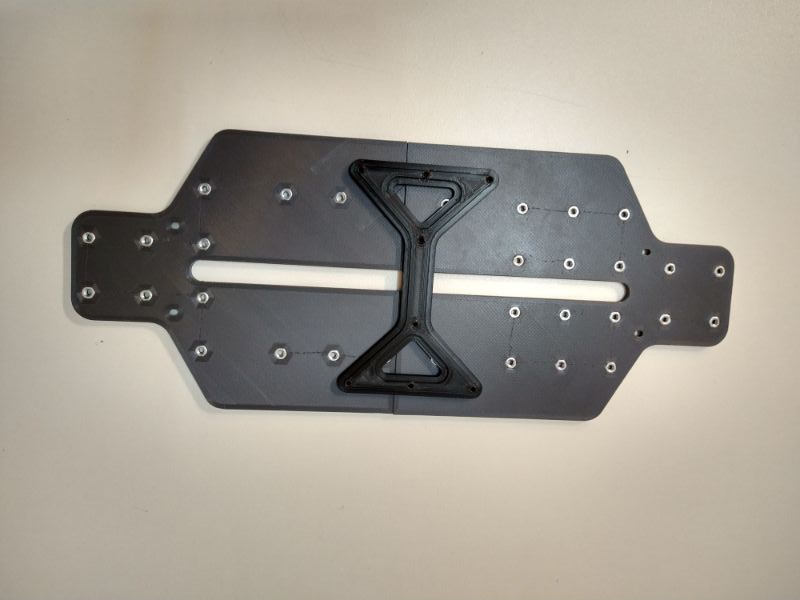
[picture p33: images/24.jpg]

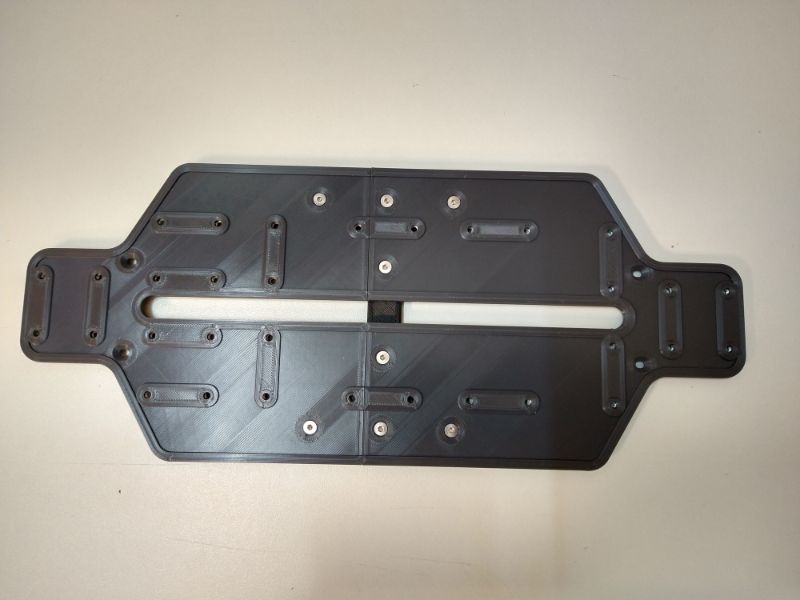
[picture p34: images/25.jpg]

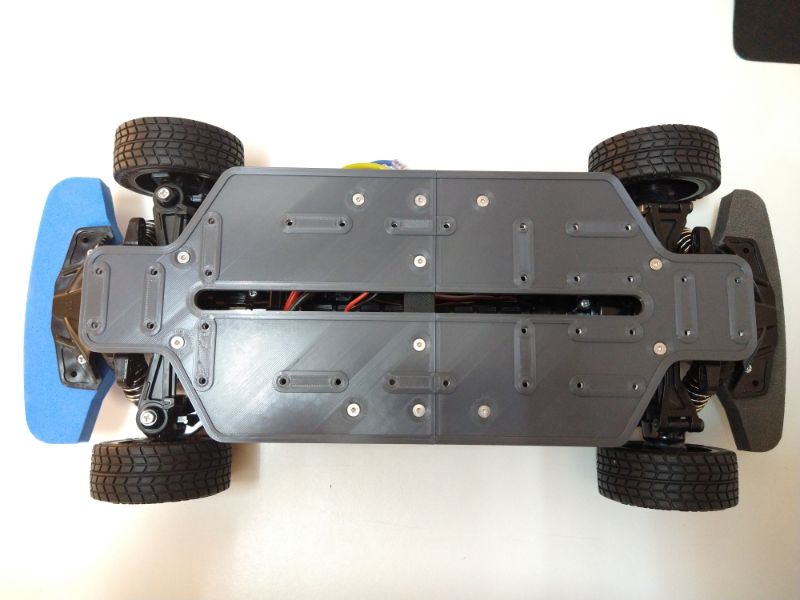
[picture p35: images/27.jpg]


# Part 4: Electronics
## Wheels speed sensors and encoder disks
 
Cut the connector of 1 end of the 3-pin wires and solder them to the IR reflectance sensors (4x). 
Use the following lengths or more:

- 2x 50cm (rear wheels)  
- 2x 30 cm (front wheels)

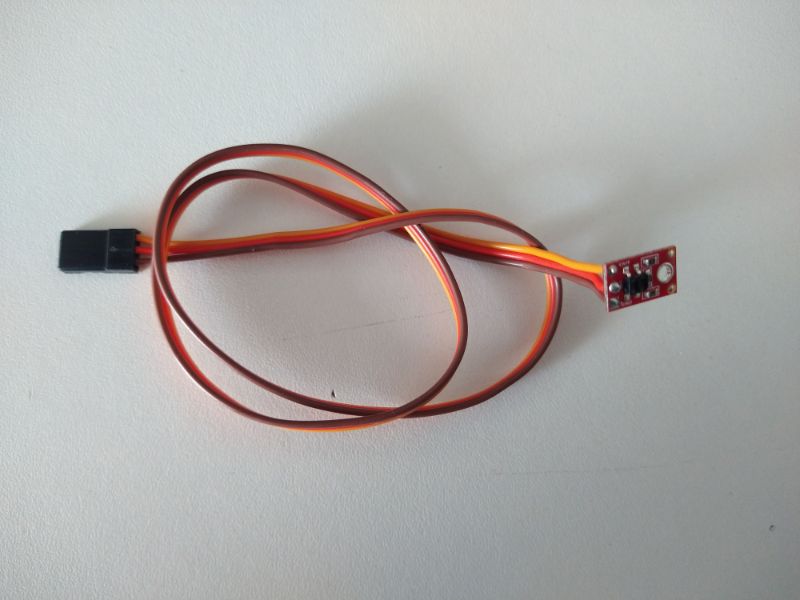
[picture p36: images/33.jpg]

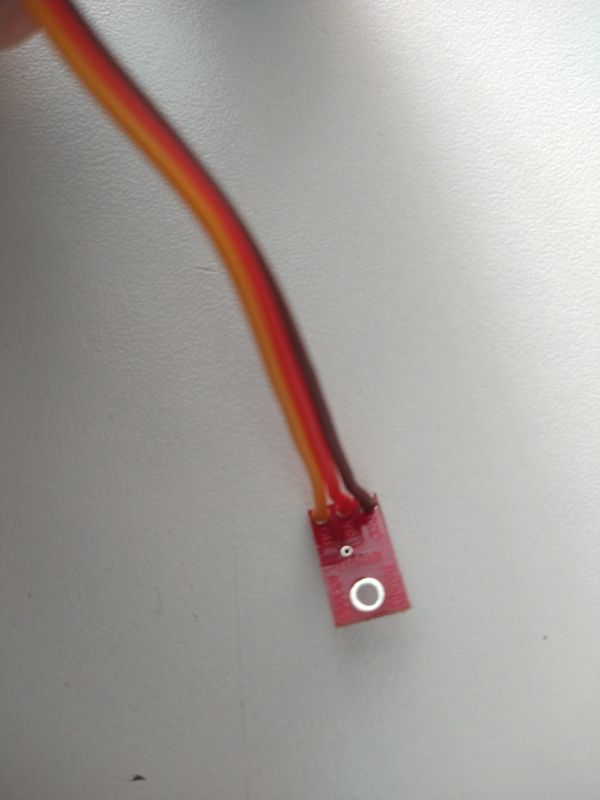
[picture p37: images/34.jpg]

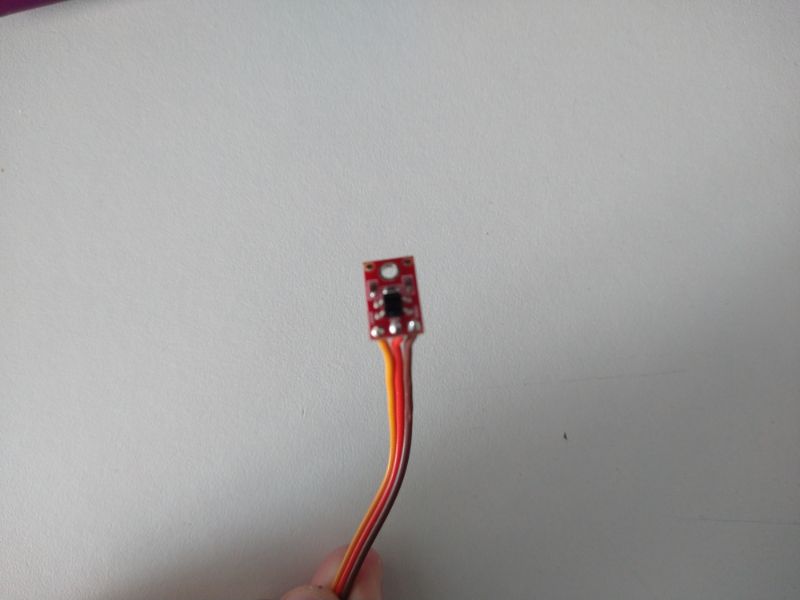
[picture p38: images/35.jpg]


Remove the wheels and the standard wheel carriers. Use hot glue to secure the sensor mounts in the orientation as shown, with the mounting plate facing **down** and **away** from the center. It may be necessary to trim some of the excess material on the wheel hubs.

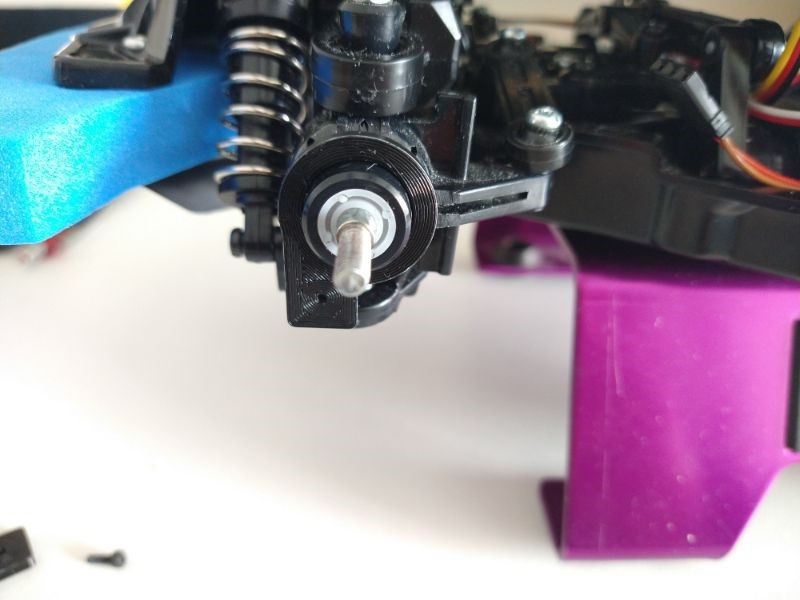
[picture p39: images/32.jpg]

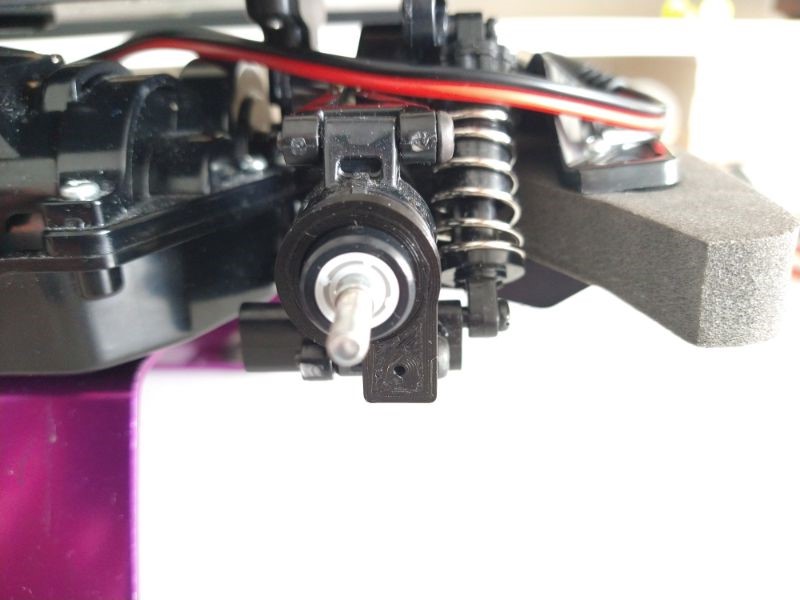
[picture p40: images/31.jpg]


Bolt the sensors to the wheel hubs with M2x6 bolts and zip tie the wires to the linkages for some strain relief for the solder connections:

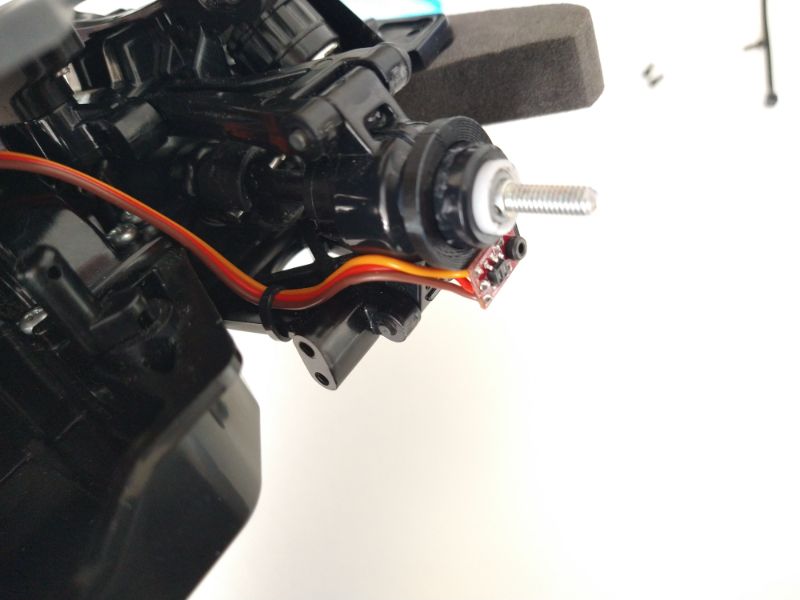
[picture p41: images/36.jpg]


Cover the encoder disks with aluminium foil or similar with good IR reflectivity, and mount them on the axles. They will clamp in place on the original locking pin:

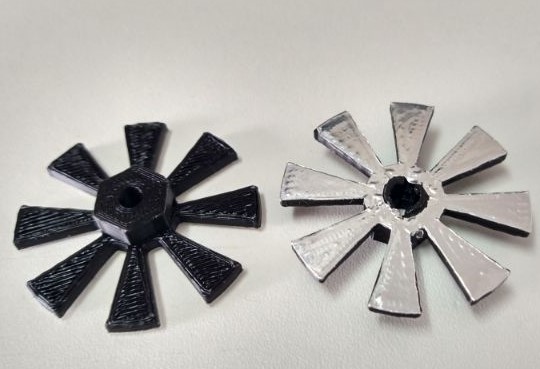
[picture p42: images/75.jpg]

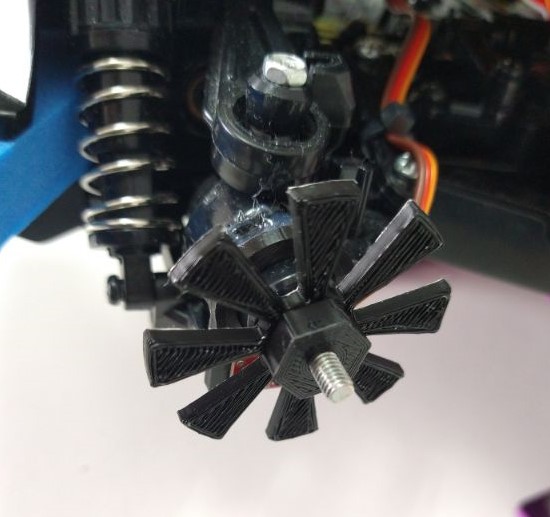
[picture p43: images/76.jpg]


## IMU, Arduino, Odroid

Screw the IMU down on the IMU support plate, and mount the support plate in the center of the deck. Do the same for the Arduino Nano shield, and the Odroid computer mount:

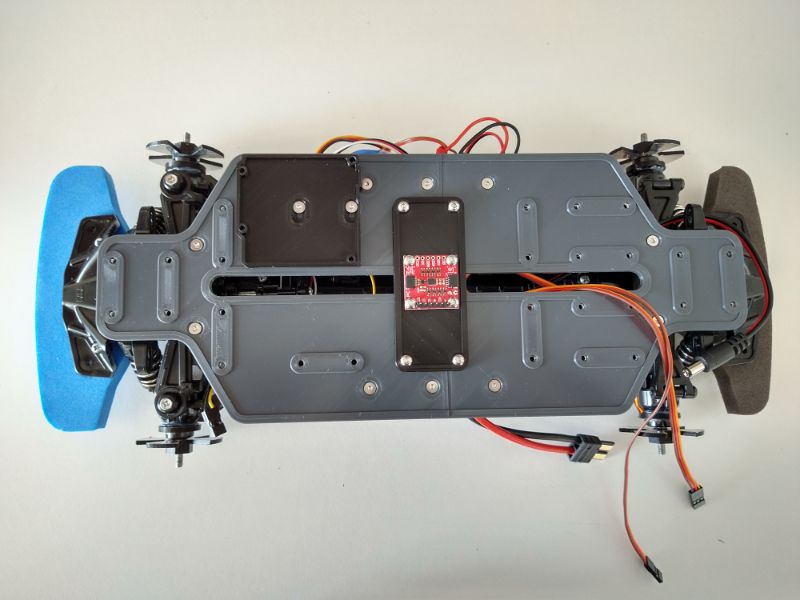
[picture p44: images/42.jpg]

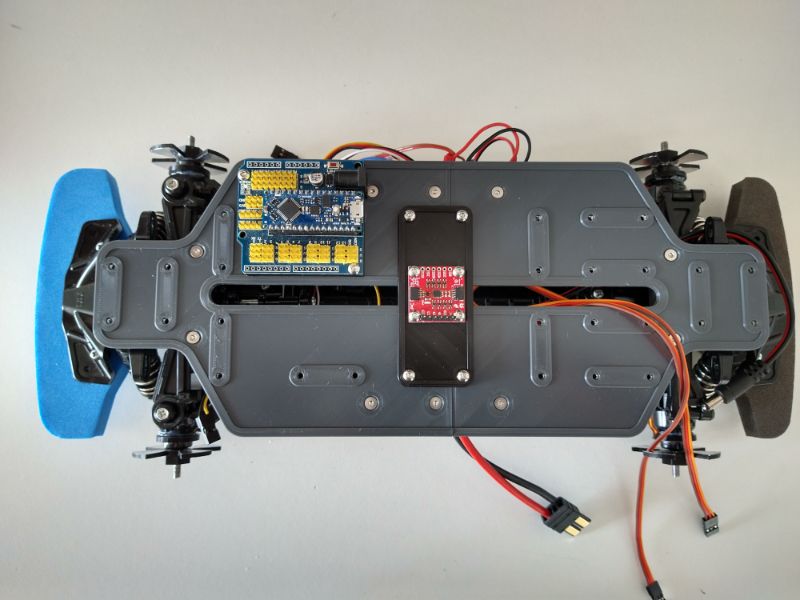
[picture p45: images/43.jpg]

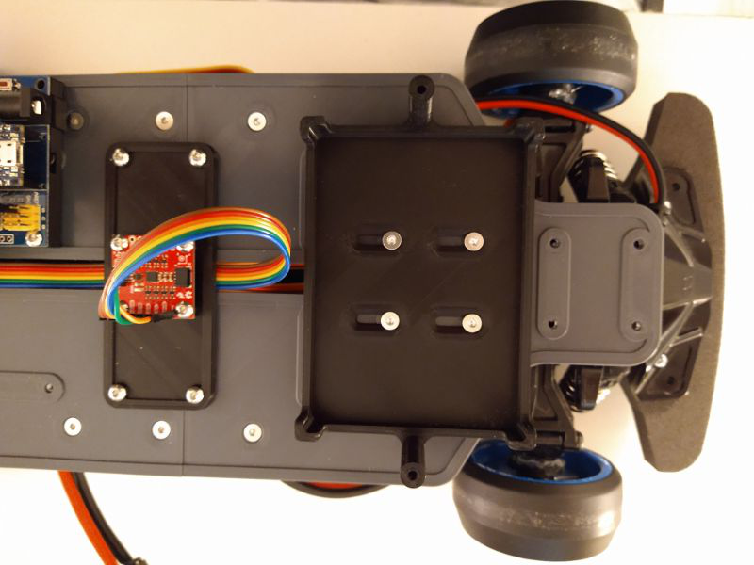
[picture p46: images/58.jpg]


## Wiring and Cable Management
Hook up the sensors to the Arduino's with the help of the [Wiring Diagram](/documentation/wiring_diagram.md).

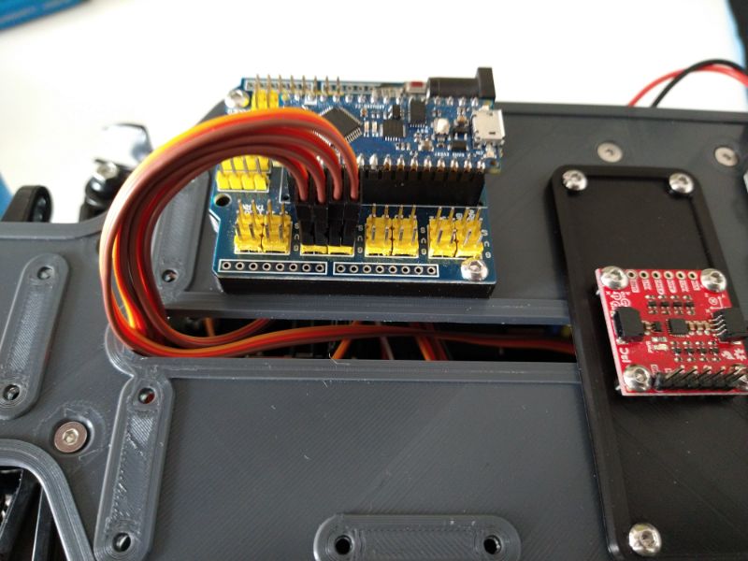
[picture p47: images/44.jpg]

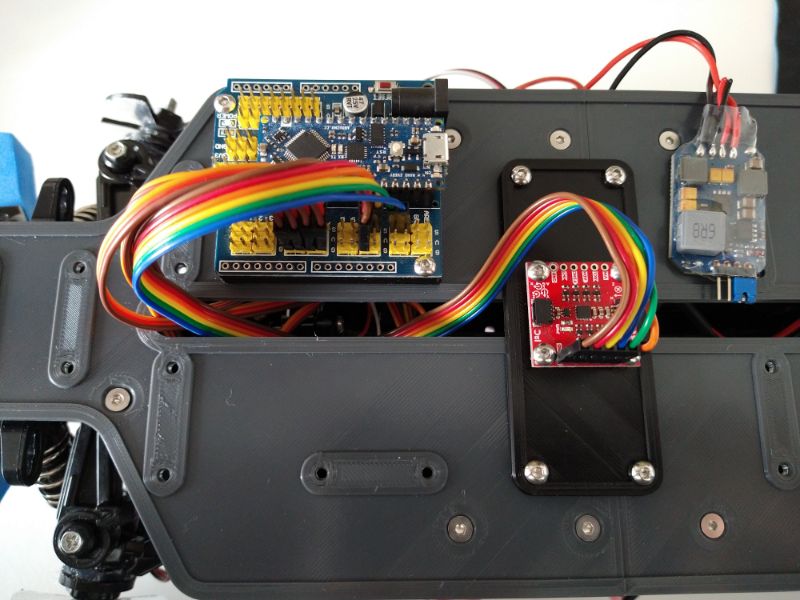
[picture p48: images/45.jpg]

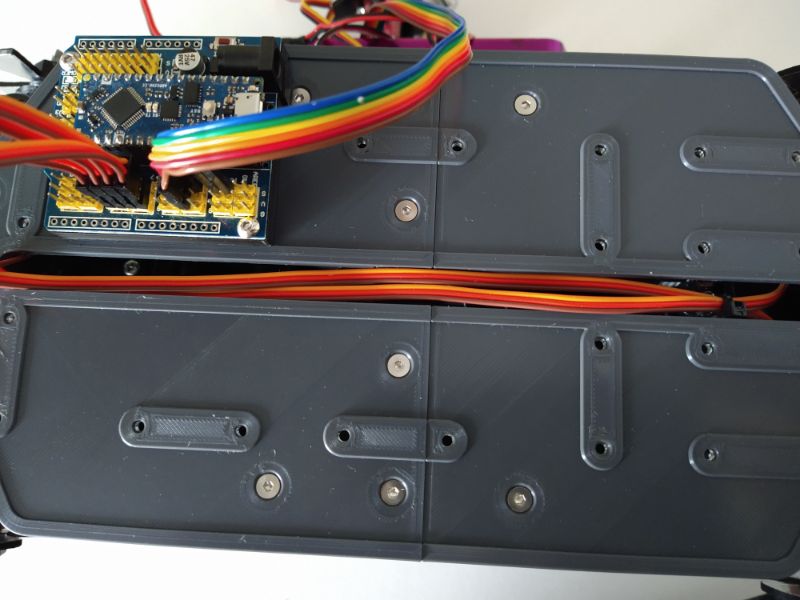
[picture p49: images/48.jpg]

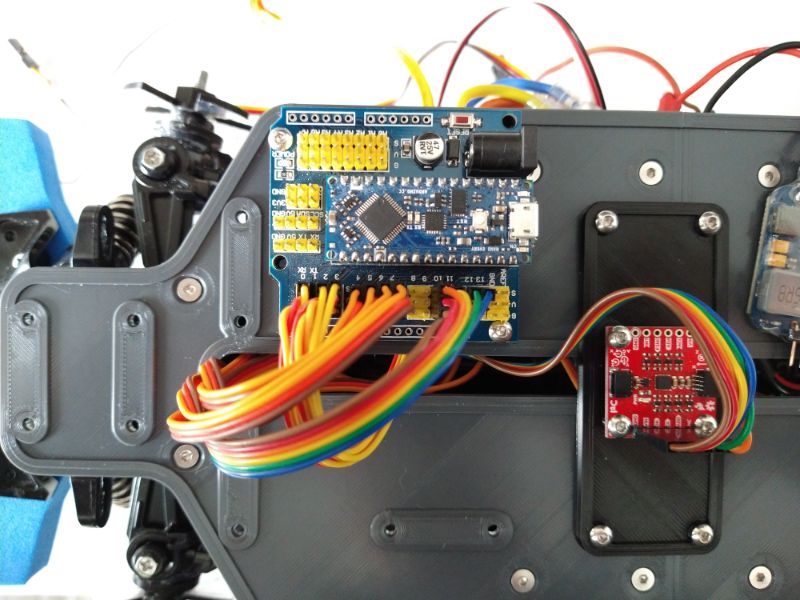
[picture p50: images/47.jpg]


It is important that all wires are clear of the moving parts of the vehicle. This applies mainly to the center driveshaft and the steering linkages.
The DC-DC converter can be zip tied to the motor wires under the top deck:

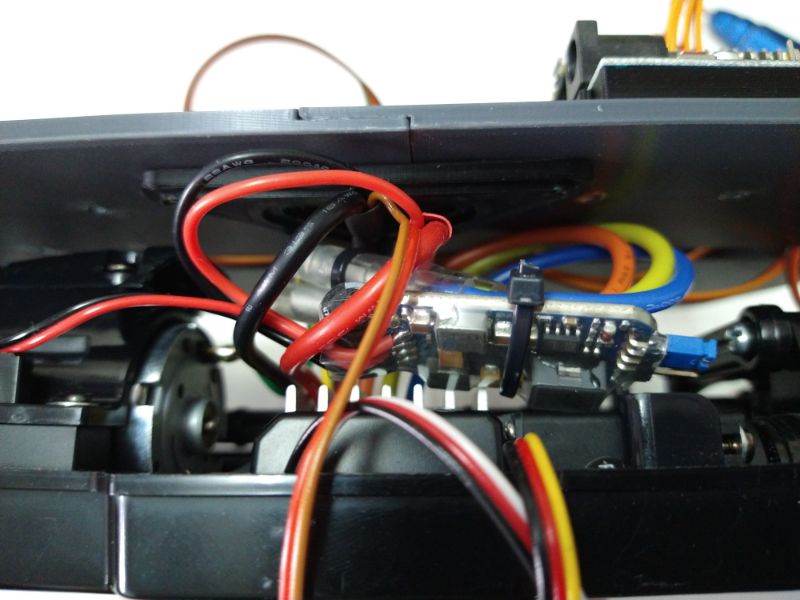
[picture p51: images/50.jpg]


The encoder cables and IMU cables can be secured between the IMU mounting plate and the deck brace. Tie the battery wires to the brace as well, so you are not pulling on the fragile wires when changing batteries!

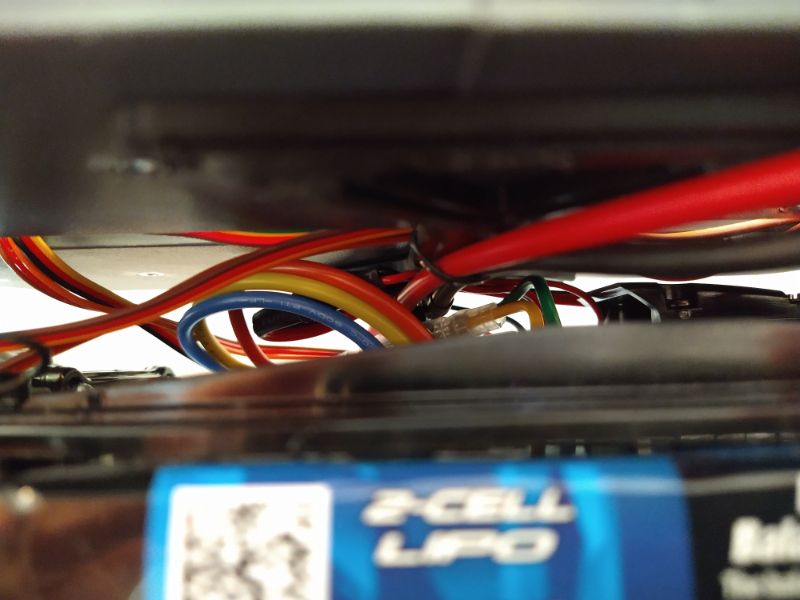
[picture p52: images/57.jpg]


RECEIVER
The receiver can be wired to the Arduino with 3x 3 pin connectors:

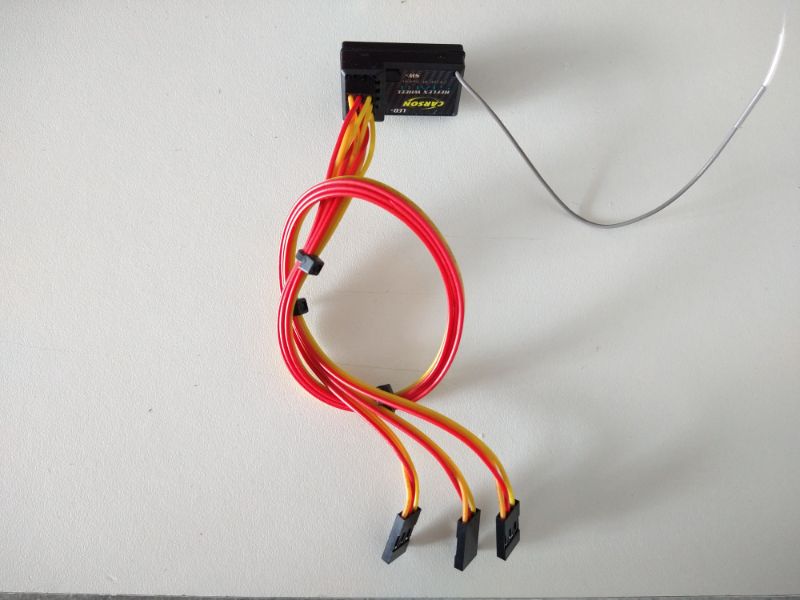
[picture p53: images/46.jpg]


Stick the receiver on top of the servo with double sided tape.

## ESC/SERVO POWER

The Tamiya ESC provides 5v power over the 3 pin conector. We will use that to power the steering servo. This is to make sure the Arduino is not powered from two different sources (USB and ESC) and the servo doesn’t draw too much power from the Arduino. 
We will remove the positive (+) pin from the 3 pin connectors and wire them together.

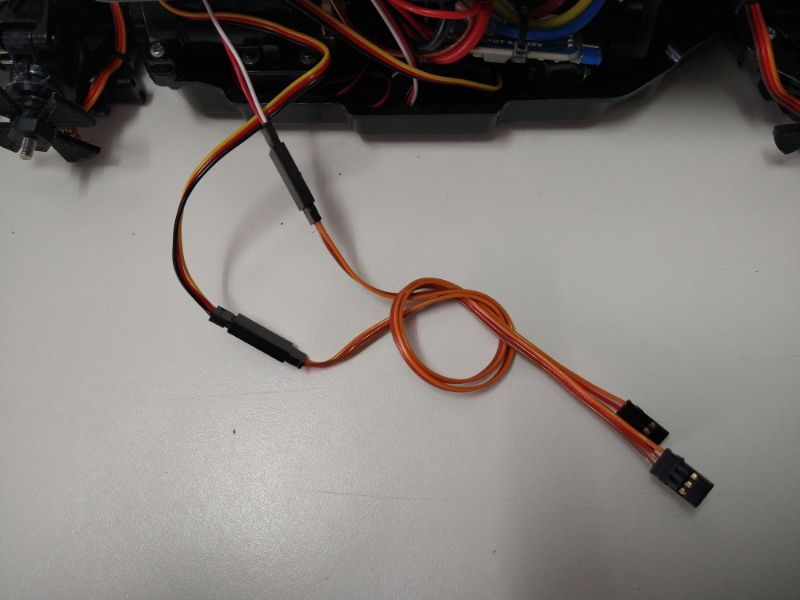
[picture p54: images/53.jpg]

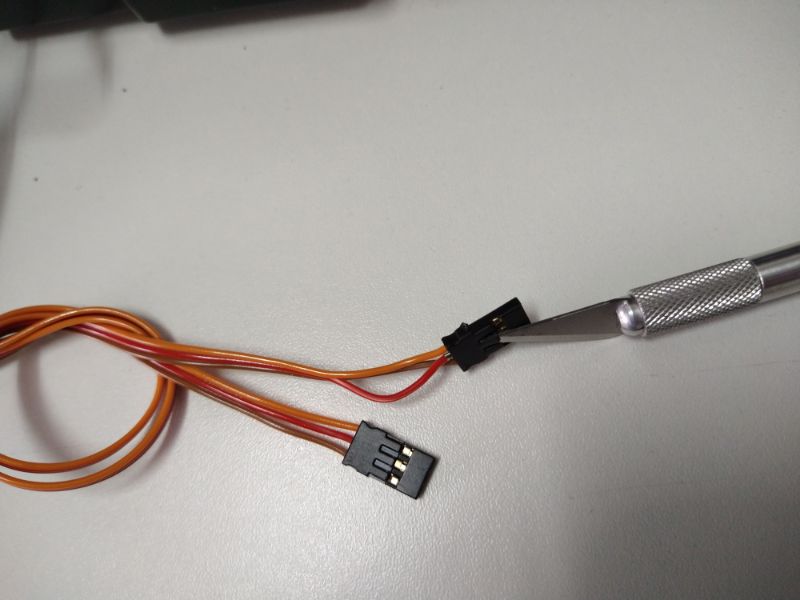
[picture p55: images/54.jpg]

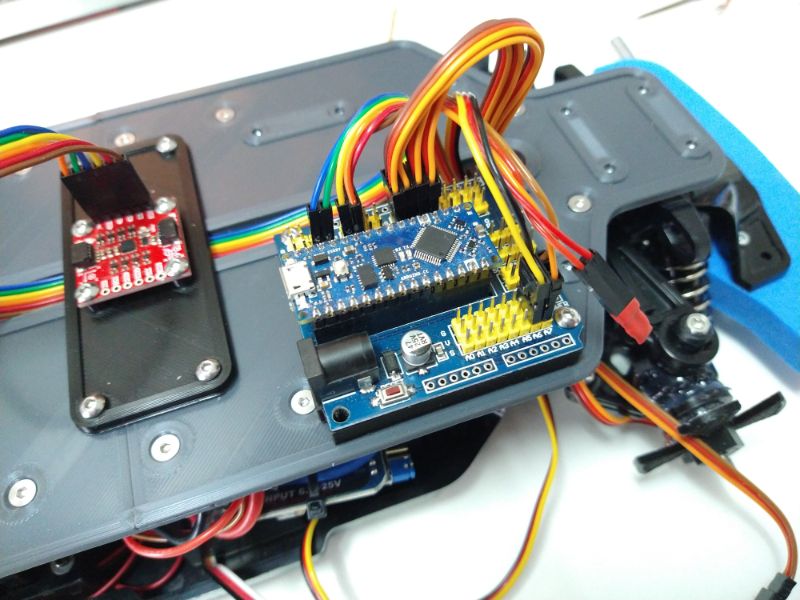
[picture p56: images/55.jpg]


2 header pins can be used to make a jumper, or the wires can be soldered together directly. Make sure the wires can not create a short on any of the components!

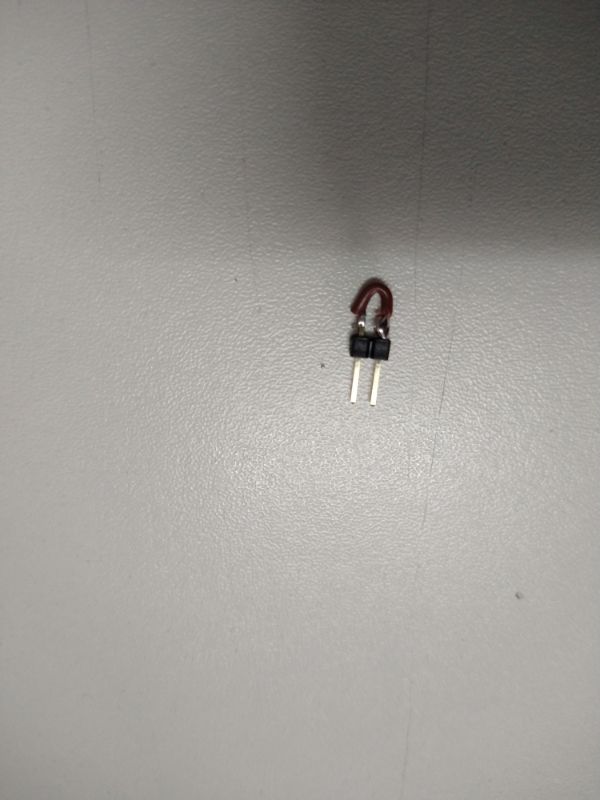
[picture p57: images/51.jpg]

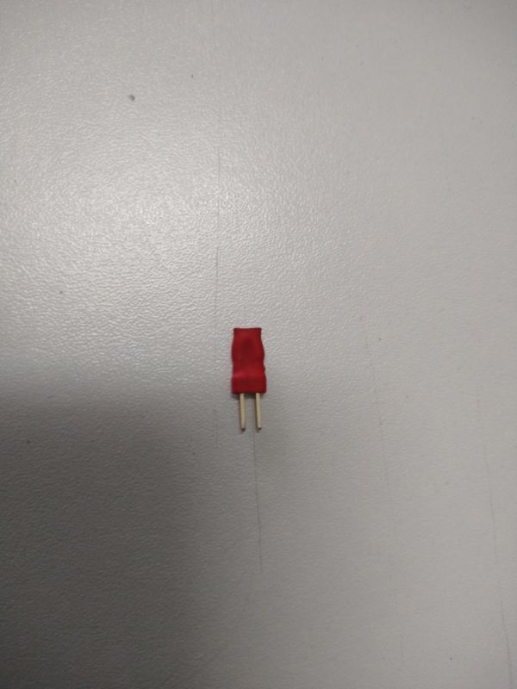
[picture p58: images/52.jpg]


## Ultrasonic Sensors

You can add aditional sensors to the car if you like. Here we will show how you can add an array of ultrasonic sensors to the vehicle. We will be using 8 HC-SR04 ultrasonic sensors.

Snap the sensors in its mounting bracket. Carefully bend the 4 pins 90 degrees so they point backwards.

Remove the screws from the IMU mounting plate, add the 'tower' for the sensors. Also, add the support for the second Arduino:

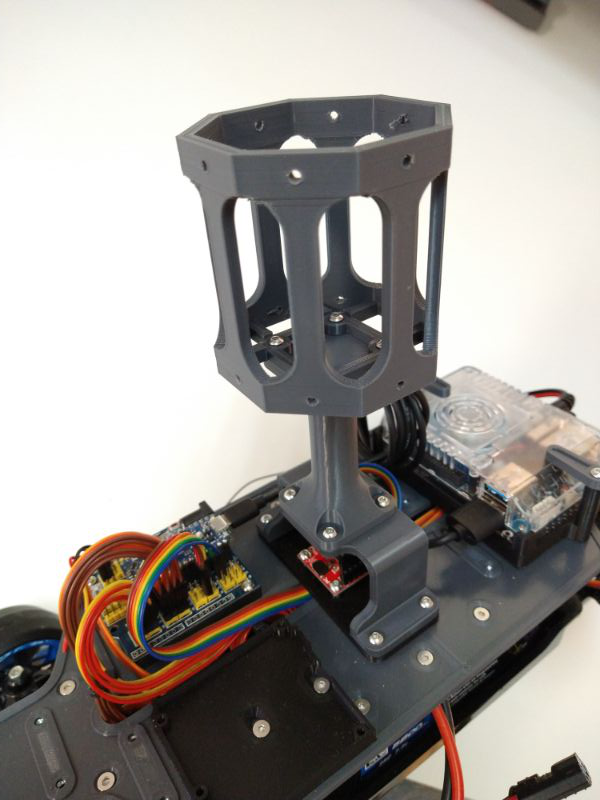
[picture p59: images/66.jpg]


The mounting brackets with the sensors can be screwed on the tower:

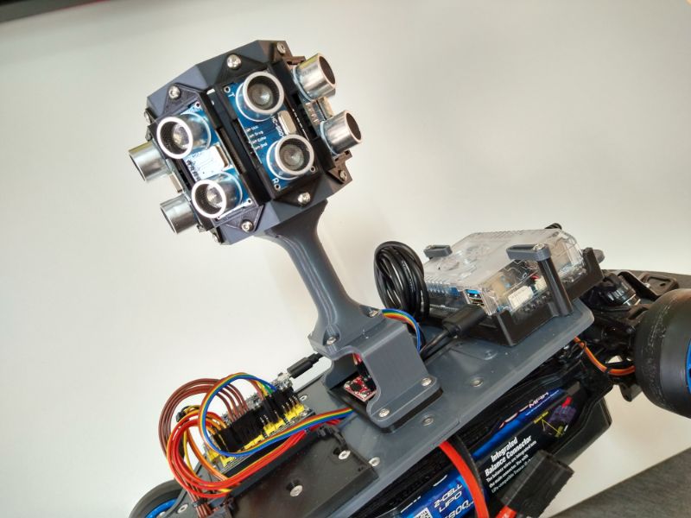
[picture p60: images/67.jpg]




The wires can be guided down trough the holes in the bottom, and to the Arduino





# Finished!

Congratulations, you can now start experimenting! Install the required [Software](/documentation/software_setup.md) to get the vehicle running.








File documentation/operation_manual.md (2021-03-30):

# Starting ROS

1. Open a terminal (Ctrl+Alt+T), and start roscore by executing the following command:
  > roscore

2. Open another terminal, and change directory to your ROS workspace:
  > cd/tu_ws
3. Source the setup.bash file in your workspace:
  > source devel/setup.bash

You can now start any of the ROS programs in your workspace.

5. To start the serial communication over USB, run the serial_launch.launch file. You can use a launch file to execute multiple ROS programs with 1 command. In this case, it launches two nodes that listen to the messages from the Arduino's.
  > roslaunch car serial_launch.launch

6. To launch a controller, -*for example controller.py*-,  repeat steps 2-3 and start your executable:
  >rosrun car controller.py

# Switching between manual and automated driving modes

When the transmitter is turned on, the vehicle is in "manual mode". This means that the control signals from the transmitter are directly sent to the servo and speed controller. You are in control of the car.

When the "CH3" button is pressed on the transmitter (transmitter panel, top left), the Arduinos will relay the commands from the Odroid on the ROS network. The vehicle is in "automatic mode". When the "CH3" button is pressed again, the vehicle returns to "manual mode".

Start the vehicle with the wheels raised off the floor. This prevents damage from the vehicle accidently driving away.

When the Arduino is powered on or reset, the accelerometer is calibrated for 5 seconds. Place the vehicle on a flat surface, reset the Arduino and do not touch the vehicle for a couple seconds.

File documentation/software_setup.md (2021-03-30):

# Software Setup

Install the following software on your Odroid XU-4.

## OS 
Start by installing a Linux image (MATE) on the computer memory. Hardkernel provides the images and a tutorial in their [Odroid Wiki](https://wiki.odroid.com/getting_started/os_installation_guide).
You will need a Micro SD card reader to connect the memory and its adapter to your PC.

Alternatively, you can buy a memory module with the OS already installed.

## WiFi Drivers
Many USB WiFi dongles are not directly supported on all Linux kernels. If your WiFi module is not working, you likely need to install your drivers manually. For the WiFi module in the [Bill of Materials](/documentation/bill_of_materials.md), use these [drivers](https://github.com/lwfinger/rtl8723bu).

## Robot Operating System (ROS)
Install the correct ROS distribution for your Linux version. [ROS](https://www.ros.org/) is used to communicate between your Arduinos and your computer. If you are unfamiliar with ROS, follow their excellent [Beginner Level turtorials](http://wiki.ros.org/ROS/Tutorials)

You can install the [package 'car'](/ros) and modify from there. 
The package is very minimal; it contains:
- Launch file for USB serial communnication
- custom messages for the vehicle state, radar state, and control actions
- a controller script that runs a Tensorflow session

## TensorFlow / TensorFlow Lite
Install [TensorFlow](https://www.tensorflow.org/) or [TensorFlow Lite](https://www.tensorflow.org/lite) if you want to execute your trained Neural Networks on the car.
Installing the full version of TensorFlow on an ARM system such as the Odroid can be difficult. Compiling the Tensorflow Wheel yourself is slow and requires some experience.
[This guide](https://www.jianshu.com/p/375cacb4c0f2) will help you to install a [precompiled ARM version](https://github.com/lhelontra/tensorflow-on-arm/releases) of TensorFlow on your Odroid XU-4.

## Remote Access
You can access your Odroid remotely over the internet. If you want to cast the entire screen of the Odroid, you can use [NoMachine](https://www.nomachine.com/). Keep in mind that remote access is slower than working on the computer directly; connect to the Odroid over USB/HDMI directly for longer sessions, or use SSH.

## Arduino

### IDE
Install the [Arduino IDE](https://www.arduino.cc/en/software/) to write code to the Arduinos.

### Libraries
Through Arduinos Library Managers, install the following libraries:
- [Rosserial library](https://www.arduino.cc/reference/en/libraries/rosserial-arduino-library/)
- [Sparkfun ICM-20948 library](https://github.com/sparkfun/SparkFun_ICM-20948_ArduinoLibrary)

The vehicle has 2 of the new Arduino Nano boards, called the Arduino Nano Every. This is a board with the new Mega-AVR architecture, instead of the standard AVR architecture of the common Uno boards. (Note: the official terminology of Mega-AVR and AVR is different between Arduino and the chip maker.) Unfortunately, many libraries are not compatible without a little care of modification.
	
For the Rosserial Library:
    Use Arduino AVR board manager 1.8.4 or older

For the Sparkfun ICM library (for the sparkfun IMU):
1.	Open ICM_20948.cpp 
2.	Go to line 750, column 35
3. 	change
> digitalWrite(_ad0, _ad0val);

to

> digitalWrite(_ad0, (PinStatus)_ad0val);

### ROS Message files
The ROS communication relies on custom messages. The library for them can be generated as follows:
Creating message.h files for Arduino:

1. cd to your Arduino library folder
2. Delete ros_lib folder if you want to re-generate
> rosrun rosserial_arduino make_libraries.py 

### Code
The code for the Arduinos can be found [here](/Arduino)

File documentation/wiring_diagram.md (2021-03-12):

# Wiring diagram for the Arduinos

## Nano1 : RC IN/OUT, ENCODERS IN, IMU IN (vehicle state)
		
		A0
		A1
		A2
		A3
		A4
		A5
		A6 = To Servo
		A7 = To Electronic Speed Controller

		1 = Steering in			(receiver channel 1)
		2 = Throttle in			(receiver channel 2)
		3 = AUX in			(receiver channel 3)

		4 = Wheel Encoder (FL)
		5 = Wheel Encoder (FR)
		6 = Wheel Encoder (RL) 
		7 = Wheel Encoder (RR)

		8 
		9 
		10 = IMU (CS,1)
		11 = IMU (MOSI,4)

		12 = IMU(MISO,2)
		13 = IMU(SCLK,3)
		GND
		AREF

## SPARKFUN IMU
		CS = NANO PIN 10
		MISO = NANO PIN 12
		SCLK = NANO PIN 13
		MOSI = NANO PIN 11
		IV8-5V5 = 5V
		GND = GND

## Nano 2 : Ultrasonic Sensor Array 

		A0 = Trigger radar 1
		A1 = Trigger radar 2
		A2 = Trigger radar 3
		A3 = Trigger radar 4
		A4 = Trigger radar 5
		A5 = Trigger radar 6
		A6 = Trigger radar 7 
		A7 = Trigger radar 8

		1
		2
		3

		4 = Echo radar 1
		5 = Echo radar 2
		6 = Echo radar 3
		7 = Echo radar 4

		8 = Echo radar 5
		9 = Echo radar 6
		10 = Echo radar 7
		11 = Echo radar 8

		12
		13
		GND
		AREF

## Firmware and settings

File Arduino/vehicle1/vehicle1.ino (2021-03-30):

// ---------------------------------------------------------------- //
// Arduino Ultrasoninc Sensor array for research vehicle
// Arduino IDE < 1.8.4
// Created for the Department of Cognitive Robotics (CoR) TuDelft
// 
// ---------------------------------------------------------------- //


#include "ICM_20948.h"  // Click here to get the library: http://librarymanager/All#SparkFun_ICM_20948_IMU
#include "math.h"
#include <Servo.h>

//ROS///////////////////////////////////////////////////////////////////////////////////
#include <ros.h>
#include <car/vehicle_state_msg.h>
#include <car/control_actions_msg.h>
ros::NodeHandle  nh;

float steering_out = 1500.00;
float throttle_out = 1500.00;
void controlCallback(const car::control_actions_msg& pwm_signals){
steering_out = pwm_signals.steering_action;
throttle_out = pwm_signals.throttle_action;    
}

car::control_actions_msg control_actions;
car::vehicle_state_msg vehicle_state;
ros::Publisher pub_vehicle("vehicle_state", &vehicle_state);
ros::Subscriber<car::control_actions_msg> sub_control_actions("control_actions", controlCallback);

long publisher_timer; 
//ROS///////////////////////////////////////////////////////////////////////////////////



#define USE_SPI       // Uncomment this to use SPI
#define SERIAL_PORT Serial
#define SPI_PORT SPI    // Your desired SPI port.       Used only when "USE_SPI" is defined
#define CS_PIN 10        // Which pin you connect CS to. Used only when "USE_SPI" is defined
#define WIRE_PORT Wire  // Your desired Wire port.      Used when "USE_SPI" is not defined
#define AD0_VAL   1     // The value of the last bit of the I2C address. 
                        // On the SparkFun 9DoF IMU breakout the default is 1, and when 
                        // the ADR jumper is closed the value becomes 0

#ifdef USE_SPI
  ICM_20948_SPI myICM;  // If using SPI create an ICM_20948_SPI object
#else
  ICM_20948_I2C myICM;  // Otherwise create an ICM_20948_I2C object
#endif

#define DEG2RAD 0.0174533
#define RAD2DEG 57.2958
#define MG2MSS 0.00981
#define pi 3.141593  
#define RPM2RADS 0.104719755


  float u = 0;
  float v = 0;
  float r = 0;
  
  float a_x = 0;
  float a_y = 0;
  float a_z = 0;
  float a_x_prev = 0;
  float a_y_prev = 0;
  float a_z_prev = 0;

  
  float g_x = 0;
  float g_y = 0;
  float g_z = 0;
  float g_x_prev = 0;
  float g_y_prev = 0;
  
  float alpha_x = 0;
  float alpha_y = 0;  
  float alpha_x_prev = 0;
  float alpha_y_prev = 0;

  float rx = 0;
  float ry = 0;
  float rz = 0;
  float rx2 = 0;
  float ry2 = 0;
  float rz2 = 0;
  
  float a_x_offset = 0;
  float a_y_offset = 0;
  float a_z_offset = 0;
  float g_x_offset = 0;
  float g_y_offset = 0;
  float g_z_offset = 0;
    
  unsigned long t1;
  unsigned long t2; 
  float dt; // Can probably be long?
 
  int STATIC_COUNT = 0;
  int accel_free = 0;

//RX,TX
Servo steering;
Servo throttle;

volatile int pwm_value_ch1 = 0;
volatile int prev_time_ch1 = 0;
volatile int pwm_value_ch2 = 0;
volatile int prev_time_ch2 = 0;
volatile int pwm_value_ch3 = 0;
volatile int prev_time_ch3 = 0;

int ST_in = 1;
int TH_in = 2;
int ST_out = A6;
int TH_out = A7;

//Wheel Encoders
#define ppr 8       //amount of encoder pulses per rotation

volatile unsigned long curr_time_fl = 0;
volatile unsigned long curr_time_fr = 0;
volatile unsigned long curr_time_rl = 0;
volatile unsigned long curr_time_rr = 0;

volatile unsigned long prev_time_fl = 0;
volatile unsigned long prev_time_fr = 0;
volatile unsigned long prev_time_rl = 0;
volatile unsigned long prev_time_rr = 0;

unsigned long system_time = 0;
#define time_limit 250000 //Timeout in micros before wheel speeds are pulled to 0

float rpm_fl = 0;
float rpm_fr = 0;
float rpm_rl = 0;
float rpm_rr = 0;


void setup() {
  //ROS///////////////////////////////////////////////////////////////////////////////////
  nh.initNode();
  nh.advertise(pub_vehicle);
  nh.subscribe(sub_control_actions);
  //ROS///////////////////////////////////////////////////////////////////////////////////

  
  // TX,RX    
  attachInterrupt(1, risingch1, RISING);
  attachInterrupt(2, risingch2, RISING);
  attachInterrupt(3, risingch3, RISING);
  pinMode(ST_in, INPUT);
  pinMode(TH_in, INPUT);

  steering.attach(ST_out);
  steering.writeMicroseconds(1500);
  throttle.attach(TH_out);
  throttle.writeMicroseconds(1500);

  //Wheel Encoders
  attachInterrupt(4, encoder_fl, RISING);
  attachInterrupt(5, encoder_fr, RISING);
  attachInterrupt(6, encoder_rl, RISING);
  attachInterrupt(7, encoder_rr, RISING);


  //Serial connection  
  SERIAL_PORT.begin(115200);
  while(!SERIAL_PORT){}; //Do nothing if serial not connected?

  #ifdef USE_SPI
    SPI_PORT.begin();
  #else
    WIRE_PORT.begin();
    WIRE_PORT.setClock(400000);
  #endif
  
  bool initialized = false;
  while( !initialized ){

  #ifdef USE_SPI
    myICM.begin( CS_PIN, SPI_PORT ); 
  #else
    myICM.begin( WIRE_PORT, AD0_VAL );
  #endif
    
    SERIAL_PORT.print( F("Initialization of the sensor returned: ") );
    SERIAL_PORT.println( myICM.statusString() );
    if( myICM.status != ICM_20948_Stat_Ok ){
      SERIAL_PORT.println( "Trying again..." );
      delay(500);
    }else{
      initialized = true;
    }
  }

  // In this advanced example we'll cover how to do a more fine-grained setup of your sensor
  SERIAL_PORT.println("Device connected!");

  // Here we are doing a SW reset to make sure the device starts in a known state
  myICM.swReset( );
  if( myICM.status != ICM_20948_Stat_Ok){
    SERIAL_PORT.print(F("Software Reset returned: "));
    SERIAL_PORT.println(myICM.statusString());
  }
  delay(250);
  
  // Now wake the sensor up
  myICM.sleep( false );
  myICM.lowPower( false );

  // The next few configuration functions accept a bit-mask of sensors for which the settings should be applied.

  // Set Gyro and Accelerometer to a particular sample mode
  // options: ICM_20948_Sample_Mode_Continuous
  //          ICM_20948_Sample_Mode_Cycled
  myICM.setSampleMode( (ICM_20948_Internal_Acc | ICM_20948_Internal_Gyr), ICM_20948_Sample_Mode_Continuous ); 
  if( myICM.status != ICM_20948_Stat_Ok){
    SERIAL_PORT.print(F("setSampleMode returned: "));
    SERIAL_PORT.println(myICM.statusString());
  }

  // Set full scale ranges for both acc and gyr
  ICM_20948_fss_t myFSS;  // This uses a "Full Scale Settings" structure that can contain values for all configurable sensors
  
  myFSS.a = gpm2;         // (ICM_20948_ACCEL_CONFIG_FS_SEL_e)
                          // gpm2
                          // gpm4
                          // gpm8
                          // gpm16
                          
  myFSS.g = dps500;       // (ICM_20948_GYRO_CONFIG_1_FS_SEL_e)
                          // dps250
                          // dps500
                          // dps1000
                          // dps2000
                          
  myICM.setFullScale( (ICM_20948_Internal_Acc | ICM_20948_Internal_Gyr), myFSS );  
  if( myICM.status != ICM_20948_Stat_Ok){
    SERIAL_PORT.print(F("setFullScale returned: "));
    SERIAL_PORT.println(myICM.statusString());
  }


  // Set up Digital Low-Pass Filter configuration
  ICM_20948_dlpcfg_t myDLPcfg;            // Similar to FSS, this uses a configuration structure for the desired sensors
  myDLPcfg.a = acc_d473bw_n499bw;         // (ICM_20948_ACCEL_CONFIG_DLPCFG_e)
                                          // acc_d246bw_n265bw      - means 3db bandwidth is 246 hz and nyquist bandwidth is 265 hz
                                          // acc_d111bw4_n136bw
                                          // acc_d50bw4_n68bw8
                                          // acc_d23bw9_n34bw4
                                          // acc_d11bw5_n17bw
                                          // acc_d5bw7_n8bw3        - means 3 db bandwidth is 5.7 hz and nyquist bandwidth is 8.3 hz
                                          // acc_d473bw_n499bw

  myDLPcfg.g = gyr_d361bw4_n376bw5;       // (ICM_20948_GYRO_CONFIG_1_DLPCFG_e)
                                          // gyr_d196bw6_n229bw8
                                          // gyr_d151bw8_n187bw6
                                          // gyr_d119bw5_n154bw3
                                          // gyr_d51bw2_n73bw3
                                          // gyr_d23bw9_n35bw9
                                          // gyr_d11bw6_n17bw8
                                          // gyr_d5bw7_n8bw9
                                          // gyr_d361bw4_n376bw5
                                          
  myICM.setDLPFcfg( (ICM_20948_Internal_Acc | ICM_20948_Internal_Gyr), myDLPcfg );
  if( myICM.status != ICM_20948_Stat_Ok){
    SERIAL_PORT.print(F("setDLPcfg returned: "));
    SERIAL_PORT.println(myICM.statusString());
  }

  // Choose whether or not to use DLPF
  // Here we're also showing another way to access the status values, and that it is OK to supply individual sensor masks to these functions
  ICM_20948_Status_e accDLPEnableStat = myICM.enableDLPF( ICM_20948_Internal_Acc, true );
  ICM_20948_Status_e gyrDLPEnableStat = myICM.enableDLPF( ICM_20948_Internal_Gyr, true );
  SERIAL_PORT.print(F("Enable DLPF for Accelerometer returned: ")); SERIAL_PORT.println(myICM.statusString(accDLPEnableStat));
  SERIAL_PORT.print(F("Enable DLPF for Gyroscope returned: ")); SERIAL_PORT.println(myICM.statusString(gyrDLPEnableStat));

  SERIAL_PORT.println();
  SERIAL_PORT.println(F("Configuration complete!")); 
 

  // Calibration procedure
 delay(500);
  if( myICM.dataReady() ){        
    for (int i = 0; i <= 9999; i++) {
      myICM.getAGMT();     
      a_x_offset += myICM.accX();
      a_y_offset += myICM.accY();
      a_z_offset += myICM.accZ()-1000;
      g_x_offset += myICM.gyrX();
      g_y_offset += myICM.gyrY();
      g_z_offset += myICM.gyrZ();
    }
  }else{
    Serial.println("Not Calibrated!");
  }  
  a_x_offset/=10000;
  a_y_offset/=10000;
  a_z_offset/=10000;
  g_x_offset/=10000;
  g_y_offset/=10000;
  g_z_offset/=10000;
  
  
  
}


void loop() {
  
  // RX,TX
  if (pwm_value_ch3 > 1500){    // manual steering and throttle control       
       steering.writeMicroseconds(pwm_value_ch1); 
       throttle.writeMicroseconds(pwm_value_ch2);        
  }else{
       steering.writeMicroseconds(steering_out); 
       throttle.writeMicroseconds(throttle_out); 
  }

  //Wheel Encoders
  system_time = micros();
  if (curr_time_fl+time_limit>system_time){ //If last update not too long ago
    rpm_fl = (1/((curr_time_fl-prev_time_fl)*0.000001))*60/ppr;
    }
    else{  // pull RPM to 0
    rpm_fl = 0;
    }    
  if (curr_time_fr+time_limit>system_time){ //If last update not too long ago
    rpm_fr = (1/((curr_time_fr-prev_time_fr)*0.000001))*60/ppr;
    }
    else{
    rpm_fr = 0;
    }      
  if (curr_time_rl+time_limit>system_time){ //If last update not too long ago
    rpm_rl = (1/((curr_time_rl-prev_time_rl)*0.000001))*60/ppr;
    }
    else{
    rpm_rl = 0;
    }
  if (curr_time_rr+time_limit>system_time){ //If last update not too long ago
    rpm_rr = (1/((curr_time_rr-prev_time_rr)*0.000001))*60/ppr;
    }
    else{
    rpm_rr = 0;
    }  

  // Get sensor values
  myICM.getAGMT();                // The values are only updated when you call 'getAGMT'  
  a_x = (myICM.accX());//-a_x_offset;
  a_y = (myICM.accY());//-a_y_offset;
  a_z = (myICM.accZ());//-a_z_offset;
  g_x = myICM.gyrX()-g_x_offset;
  g_y = myICM.gyrY()-g_y_offset;
  g_z = myICM.gyrZ()-g_z_offset;
  
  t2 = micros();
  dt = (t2-t1)/1000000.0;   
  t1 = t2; // Update t1 for next iteration

  if (sqrt(a_x*a_x+a_y*a_y+a_z*a_z)<1025) {
    STATIC_COUNT +=1;
  }else{
    STATIC_COUNT = 0;      
  }
      
  if (STATIC_COUNT > 4){
    u = 0;
    v = 0;
    accel_free = 1;
  }else{
    accel_free=0;
  }

  if (accel_free ==1){
    alpha_x = 0.95*(alpha_x+(g_x_prev+0.5*(g_x-g_x_prev))*dt)+0.05*(atan2(a_y,a_z)*RAD2DEG); //angles in deg
    alpha_y = 0.95*(alpha_y+(g_y_prev+0.5*(g_y-g_y_prev))*dt)+0.05*(-atan2(a_x,a_z)*RAD2DEG);
  }else{
    alpha_x += (g_x_prev+0.5*(g_x-g_x_prev))*dt;
    alpha_y += (g_y_prev+0.5*(g_y-g_y_prev))*dt;
    }

  g_x_prev = g_x;
  g_y_prev = g_y; 


  //rotate over x axis
  rx = a_x;
  ry = cos(alpha_x*DEG2RAD)*a_y - sin(alpha_x*DEG2RAD)*a_z;
  rz = sin(alpha_x*DEG2RAD)*a_y + cos(alpha_x*DEG2RAD)*a_z;

  //rotate over y axis
  rx2 = cos(alpha_y*DEG2RAD)*rx + sin(alpha_y*DEG2RAD)*rz;
  ry2 = ry;
  rz2 = -sin(alpha_y*DEG2RAD)*rx + cos(alpha_y*DEG2RAD)*rz;

  //convert from mg to m/s
  a_x = rx2*MG2MSS;
  a_y = ry2*MG2MSS;

  u += (a_x_prev+0.5*(a_x-a_x_prev))*dt; //First order integration with linear interpolation
  v += (a_y_prev+0.5*(a_y-a_y_prev))*dt;
  r = g_z*DEG2RAD;
  
  a_x_prev = a_x; //save 
  a_y_prev = a_y;

 

    //ROS///////////////////////////////////////////////////////////////////////////////////

      if (micros() > publisher_timer) {
      publisher_timer = micros() + 40000;
      
      vehicle_state.u = u;
      vehicle_state.v = v;
      vehicle_state.r = r;

      vehicle_state.a_x = a_x;
      vehicle_state.a_y = a_y;

      vehicle_state.omega_fl = rpm_fl*RPM2RADS;
      vehicle_state.omega_fr = rpm_fr*RPM2RADS;
      vehicle_state.omega_rl = rpm_rl*RPM2RADS;
      vehicle_state.omega_rr = rpm_rr*RPM2RADS;
      
      pub_vehicle.publish(&vehicle_state);
      }
      nh.spinOnce();
    //ROS///////////////////////////////////////////////////////////////////////////////////

  
    
}

void risingch1() {
  attachInterrupt(1, fallingch1, FALLING);
  prev_time_ch1 = micros();
} 
void fallingch1() {
  attachInterrupt(1, risingch1, RISING);
  pwm_value_ch1 = micros()-prev_time_ch1;
}
void risingch2() {
  attachInterrupt(2, fallingch2, FALLING);
  prev_time_ch2 = micros();
}
void fallingch2() {
  attachInterrupt(2, risingch2, RISING);
  pwm_value_ch2 = micros()-prev_time_ch2;
}
void risingch3() {
  attachInterrupt(3, fallingch3, FALLING);
  prev_time_ch3 = micros();
} 
void fallingch3() {
  attachInterrupt(3, risingch3, RISING);
  pwm_value_ch3 = micros()-prev_time_ch3;
}

void encoder_fl() {
  prev_time_fl = curr_time_fl;
  curr_time_fl = micros();  
}
void encoder_fr() {
  prev_time_fr = curr_time_fr;
  curr_time_fr = micros();
}
void encoder_rl() {
  prev_time_rl = curr_time_rl;
  curr_time_rl = micros();
}
void encoder_rr() {
  prev_time_rr = curr_time_rr;
  curr_time_rr = micros();
}

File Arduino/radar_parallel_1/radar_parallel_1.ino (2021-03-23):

// ---------------------------------------------------------------- //
// Arduino Ultrasoninc Sensor array for research vehicle
// Arduino IDE < 1.8.4
// Using HC-SR04 Module
// Created for the Department of Cognitive Robotics (CoR) TuDelft
// ---------------------------------------------------------------- //

// Triggering all sensors at the same time on common trigger pin

#define trigPin A0      // common trigger pin

#define echoPin1 4      // echo pin sensor 1
#define echoPin2 5      // echo pin sensor 2
#define echoPin3 6      // echo pin sensor 3
#define echoPin4 7      // echo pin sensor 4
#define echoPin5 8      // echo pin sensor 5
#define echoPin6 9      // echo pin sensor 6
#define echoPin7 10     // echo pin sensor 7
#define echoPin8 11     // echo pin sensor 8

bool waiting = false;   // Time-out condition
unsigned long distances[] = {401,402,403,404,405,406,407,408};
volatile unsigned long durations[] = {1,2,3,4,5,6,7,8};
volatile unsigned long echostarttimes[] = {1,2,3,4,5,6,7,8};
unsigned long trigger_time = 10;  // store trigger time

//ROS///////////////////////////////////////////////////////////////////////////////////
#include <ros.h>
#include <car/radar_state_msg.h>
ros::NodeHandle  nh;
car::radar_state_msg  radar_state;
ros::Publisher pub_radar("radar_state", &radar_state); //function, topic, msg

long publisher_timer;  // store ROS publish time
//ROS///////////////////////////////////////////////////////////////////////////////////

void setup() {
    //ROS///////////////////////////////////////////////////////////////////////////////////
    nh.initNode();
    nh.advertise(pub_radar);
    //ROS///////////////////////////////////////////////////////////////////////////////////  
    pinMode(trigPin, OUTPUT); 
    Serial.begin(115200); // 
}



void loop() {

  if (micros()>trigger_time+40000){ // 25 times a second
    
      //Calculate distances and publish
      for(int i = 0; i < 8; i++){
      distances[i] = durations[i]/2 *0.034; 
      }
      
      //ROS///////////////////////////////////////////////////////////////////////////////////
      radar_state.radar1 = distances[0];
      radar_state.radar2 = distances[1];
      radar_state.radar3 = distances[2];
      radar_state.radar4 = distances[3];
      radar_state.radar5 = distances[4];
      radar_state.radar6 = distances[5];
      radar_state.radar7 = distances[6];
      radar_state.radar8 = distances[7];
      
      pub_radar.publish(&radar_state); 
      //ROS///////////////////////////////////////////////////////////////////////////////////    




    for(int i = 0; i < 8; i++){ 
      durations[i] = 800/0.034;
      }
         
    waiting = true; //reset time out condition    
    digitalWrite(trigPin, LOW);   // Clears the trigPin condition
    delayMicroseconds(2);    
    digitalWrite(trigPin, HIGH);  // Sets the trigPin HIGH (ACTIVE) for 10 microseconds
    delayMicroseconds(10);
    digitalWrite(trigPin, LOW);
    
    attachInterrupt(echoPin1, echo1rising, RISING);         //listen for responses
    attachInterrupt(echoPin2, echo2rising, RISING);
    attachInterrupt(echoPin3, echo3rising, RISING);
    attachInterrupt(echoPin4, echo4rising, RISING);
    attachInterrupt(echoPin5, echo5rising, RISING);
    attachInterrupt(echoPin6, echo6rising, RISING);     
    attachInterrupt(echoPin7, echo7rising, RISING);
    attachInterrupt(echoPin8, echo8rising, RISING);        
    trigger_time = micros();
    }

  if ((micros()>trigger_time+(800/0.034)) && (waiting)){    //trigger timeout if no responce is received
    detachInterrupt(echoPin1);
    detachInterrupt(echoPin2);
    detachInterrupt(echoPin3);
    detachInterrupt(echoPin4);
    detachInterrupt(echoPin5);
    detachInterrupt(echoPin6);     
    detachInterrupt(echoPin7);
    detachInterrupt(echoPin8);
    waiting = false;                                        // Make sure it only times out once.
  };

  
  //ROS///////////////////////////////////////////////////////////////////////////////////
  nh.spinOnce();
  //ROS///////////////////////////////////////////////////////////////////////////////////

}


void echo1rising(){
  attachInterrupt(echoPin1, echo1falling, FALLING); 
  echostarttimes[0] = micros();
}
void echo1falling(){
  durations[0]= micros()-echostarttimes[0];
}

void echo2rising(){
  attachInterrupt(echoPin2, echo2falling, FALLING); 
  echostarttimes[1] = micros();
}
void echo2falling(){
    durations[1]= micros()-echostarttimes[1];
}

void echo3rising(){
  attachInterrupt(echoPin3, echo3falling, FALLING); 
  echostarttimes[2] = micros();
}
void echo3falling(){
  durations[2]= micros()-echostarttimes[2];
}

void echo4rising(){
  attachInterrupt(echoPin4, echo4falling, FALLING); 
  echostarttimes[3] = micros();
}
void echo4falling(){
  durations[3]= micros()-echostarttimes[3];
}

void echo5rising(){
  attachInterrupt(echoPin5, echo5falling, FALLING); 
  echostarttimes[4] = micros();
}
void echo5falling(){
  durations[4]= micros()-echostarttimes[4];
}

void echo6rising(){
  attachInterrupt(echoPin6, echo6falling, FALLING); 
  echostarttimes[5] = micros();
}
void echo6falling(){
  durations[5]= micros()-echostarttimes[5];
}

void echo7rising(){
  attachInterrupt(echoPin7, echo7falling, FALLING); 
  echostarttimes[6] = micros();
}
void echo7falling(){
  durations[6]= micros()-echostarttimes[6];
}

void echo8rising(){
  attachInterrupt(echoPin8, echo8falling, FALLING); 
  echostarttimes[7] = micros();
}
void echo8falling(){
  durations[7]= micros()-echostarttimes[7];
}

//  For debugging
//  Serial.print("Distances: ");
//  Serial.print(distances[0]);
//  Serial.print(", ");
//  Serial.print(distances[1]);
//  Serial.print(", ");
//  Serial.print(distances[2]);
//  Serial.print(", ");
//  Serial.print(distances[3]);
//  Serial.print(", ");
//  Serial.print(distances[4]);
//  Serial.print(", ");
//  Serial.print(distances[5]);
//  Serial.print(", ");
//  Serial.print(distances[6]);
//  Serial.print(", ");
//  Serial.println(distances[7]);
